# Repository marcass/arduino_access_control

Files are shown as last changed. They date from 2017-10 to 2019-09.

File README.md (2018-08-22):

# arduino_access_control
* Use arduino to control access to electrically actuated devices

## Components
* Electronically actuated device (garage door/door/or anything you want to access)
* WiFi in range
* Arduino as node/client (communicates to network using ESP8266 and [WIFIESP](https://github.com/bportaluri/WiFiEsp) arduino lib)
* Arduino runs this [MQTT lib](https://github.com/256dpi/arduino-mqtt)
* A master/server that runs mosquitto and a webserver

## How it works
1. Pincode gets sent to topic for door requests (either by pinpad, mqttclient, web interface, rfid device etc)
2. Pincode checked against database of allowed users
3. Response is sent to the node (allow or deny)
4. Relay is actuated and DB is updated

## User managment
Users added, modified and deleted via webpage in webserver (https://<servername/URL>)

## Maintenace
### Initial setup
* Update doorsetup.py to reflect doors you want to control
* run `python views.py <admin username> <admin password>` You get to choose what they are!
* Stop script then run via systemd (or whaterever process manager you use)
* Populate db via web interface (login usng credentials supplied above above)

### ssl certs
Letsencrypt cert needs to be renewed periodically:
1. Open port 80 on router to webserver (need to enable ipv6 for fritzbox to allow this then disable as ISP falls apart with IPv6 used)
2. run `sudo certbot renew`
3. Disable access via port 80

## Troubleshooting
### My uwsgi won't work (upstream timeout errors in /var/log/nginx/error.log)
* `# systemclt stop door`
* running (from python dir) $ uwsgi --ini uwsgi.py
* Ctrl+C that process after testing api is delivering
* `# systemctl start door`
This seems to work

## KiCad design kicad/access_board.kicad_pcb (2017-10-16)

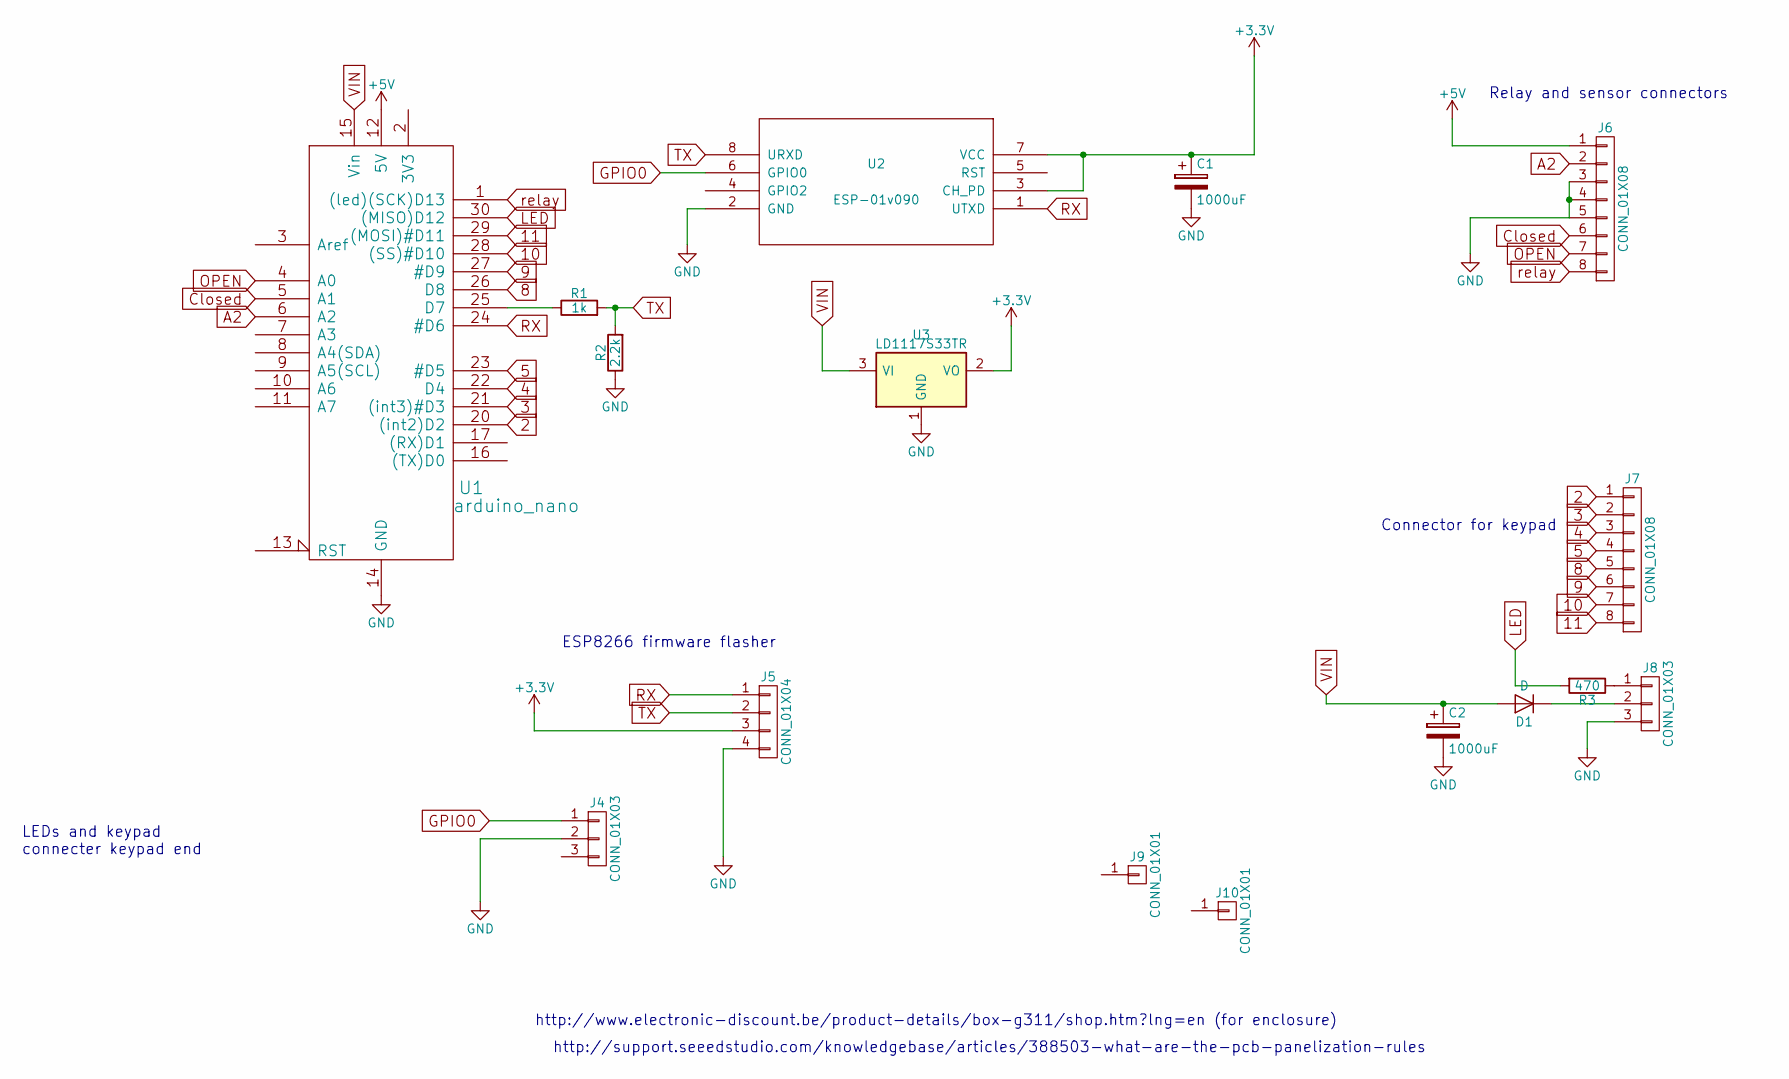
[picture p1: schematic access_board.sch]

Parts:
C1, C2: 1000uF; CP_Radial_D13.0mm_P5.00mm
D1: D; D_5W_P12.70mm_Horizontal
J4: CONN_01X03; Pin_Header_Straight_1x03_Pitch2.54mm
J5: CONN_01X04; Pin_Header_Straight_1x04_Pitch2.54mm
J6, J7: CONN_01X08; PhoenixContact_MCV-G_08x3.81mm_Vertical
J8: CONN_01X03; PhoenixContact_MCV-G_03x3.81mm_Vertical
J9, J10: CONN_01X01; MountingHole_3.2mm_M3_DIN965_Pad
R1: 1k; R_Axial_DIN0207_L6.3mm_D2.5mm_P10.16mm_Horizontal
R2: 2.2k; R_Axial_DIN0207_L6.3mm_D2.5mm_P10.16mm_Horizontal
R3: 470; R_Axial_DIN0207_L6.3mm_D2.5mm_P10.16mm_Horizontal
U1: arduino_nano; ArduinoNano
U2: ESP-01v090; ESP-01
U3: LD1117S33TR; TO-220_Vertical

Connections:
2: J7.1, U1.20 ((int2)D2)
3: J7.2, U1.21 ((int3)#D3)
4: J7.3, U1.22 (D4)
5: J7.4, U1.23 (#D5)
8: J7.5, U1.26 (D8)
9: J7.6, U1.27 (#D9)
10: J7.7, U1.28 ((SS)#D10)
11: J7.8, U1.29 ((MOSI)#D11)
+3V3: C1.1, J5.3, U2.3 (CH_PD), U2.7 (VCC), U3.2 (VO)
+5V: J6.1, U1.12 (5V)
A2: J6.2, U1.6 (A2)
Closed: J6.6, U1.5 (A1)
GND: C1.2, C2.2, J4.2, J5.4, J6.3, J6.4, J6.5, J8.3, R2.1, U1.14 (GND), U1.19 (GND), U2.2 (GND), U3.1 (GND)
GPIO0: J4.1, U2.6 (GPIO0)
LED: R3.2, U1.30 ((MISO)D12)
unnamed: D1.1 (K), J8.2
unnamed: J8.1, R3.1
unnamed: R1.1, U1.25 (D7)
OPEN: J6.7, U1.4 (A0)
RX: J5.1, U1.24 (#D6), U2.1 (UTXD)
TX: J5.2, R1.2, R2.2, U2.8 (URXD)
VIN: C2.1, D1.2 (A), U1.15 (Vin), U3.3 (VI)
relay: J6.8, U1.1 ((led)(SCK)D13)

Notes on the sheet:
ESP8266 firmware flasher
Connector for keypad
LEDs and keypad connecter keypad end
Relay and sensor connectors
http://www.electronic-discount.be/product-details/box-g311/shop.htm?lng=en (for enclosure)
http://support.seeedstudio.com/knowledgebase/articles/388503-what-are-the-pcb-panelization-rules

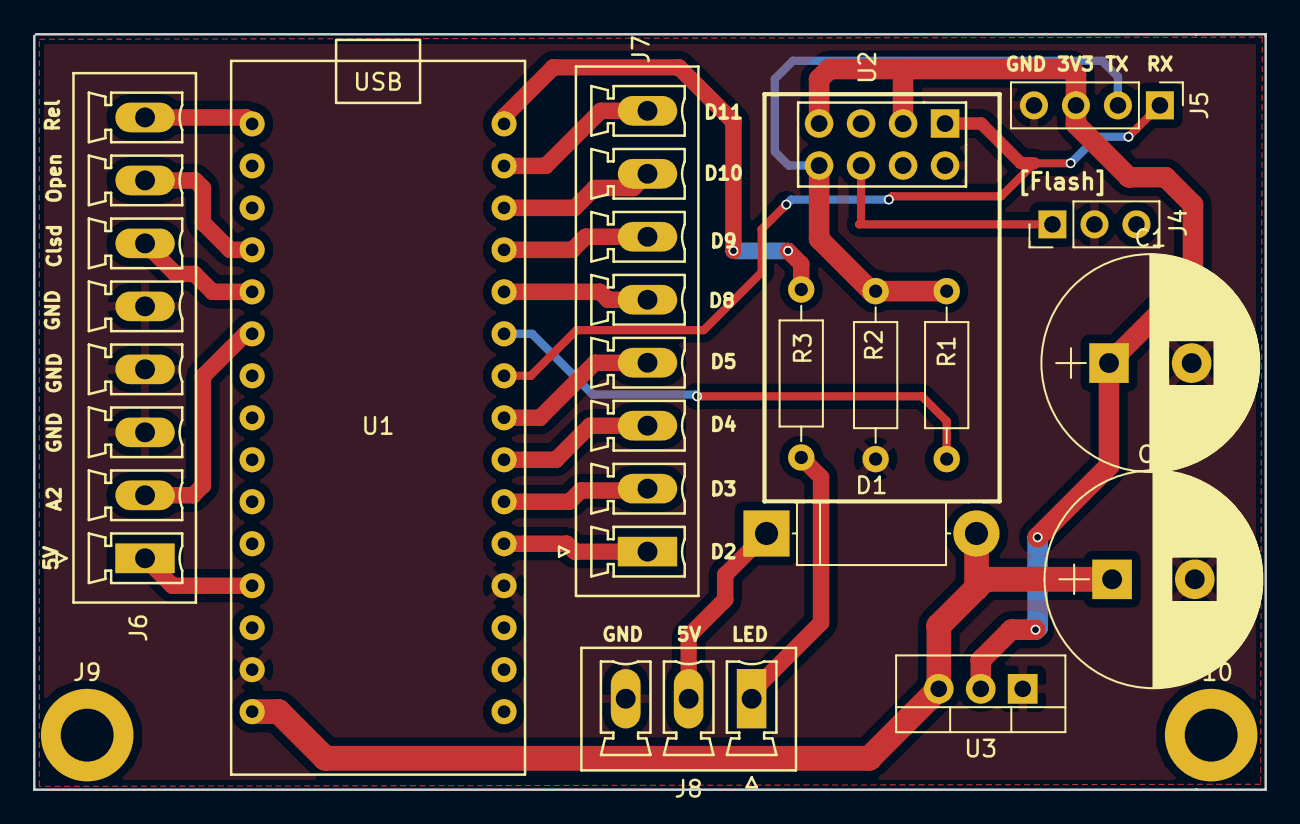
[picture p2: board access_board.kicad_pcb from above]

Board: 2 copper layers, 74.5 x 45.7 mm, 16 parts (0 on the bottom side), 23 nets.

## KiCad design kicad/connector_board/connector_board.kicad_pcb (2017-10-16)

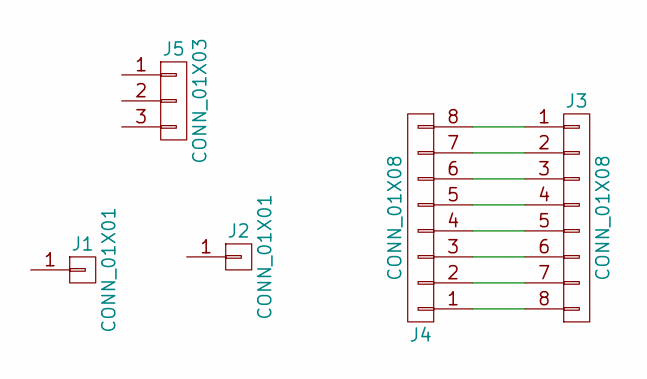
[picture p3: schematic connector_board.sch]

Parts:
J1, J2: CONN_01X01; MountingHole_3.7mm_Pad
J3: CONN_01X08; PhoenixContact_MCV-G_08x3.81mm_Vertical
J4: CONN_01X08; Pin_Header_Straight_1x08_Pitch2.54mm
J5: CONN_01X03; PhoenixContact_MCV-G_03x3.81mm_Vertical

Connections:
unnamed: J3.1, J4.8
unnamed: J3.2, J4.7
unnamed: J3.3, J4.6
unnamed: J3.4, J4.5
unnamed: J3.5, J4.4
unnamed: J3.6, J4.3
unnamed: J3.7, J4.2
unnamed: J3.8, J4.1

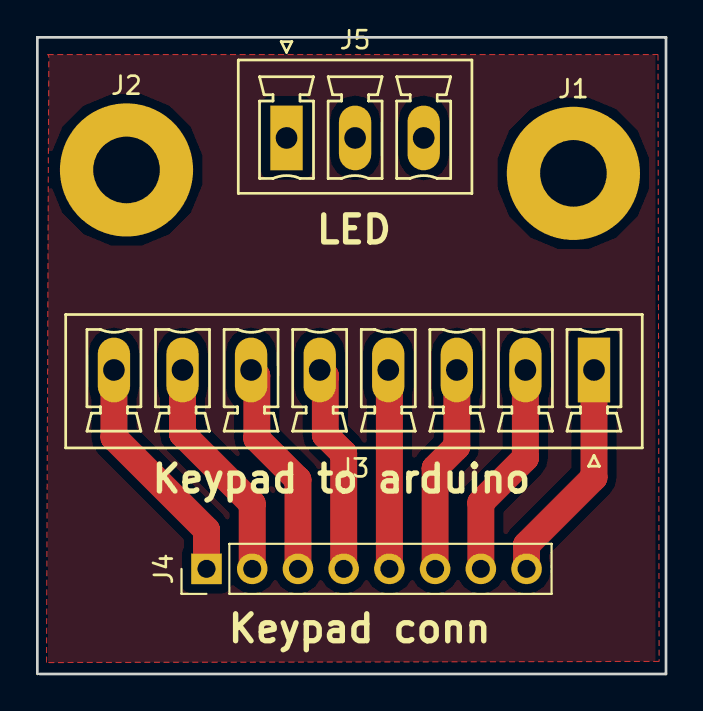
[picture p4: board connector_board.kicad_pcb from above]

Board: 2 copper layers, 34.9 x 35.4 mm, 5 parts (0 on the bottom side), 8 nets.

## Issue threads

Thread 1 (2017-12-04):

Arduino fails to connect to server

marcass, 2017-12-04:
Happens with low and unpredictable frequency. May have something to do with using alternative mqtt client to arduino itself (eg phone client)

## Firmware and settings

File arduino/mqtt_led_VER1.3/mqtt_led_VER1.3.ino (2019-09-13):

#include <SPI.h>
#include "WiFiEsp.h"
#include <Keypad.h>
//https://github.com/256dpi/arduino-mqtt
#include <MQTTClient.h>
#include <Adafruit_NeoPixel.h>

#define debug

const char DOOR[] = "bottomgarage";
const char ssid[] = "skibo";            // your network SSID (name)
const char pass[] = "r4bb1tshurtlegs";            // your network password
const char HOST[] = "192.168.0.152";
//char HOST[] = "nuc";

const char willTOPIC[] = "doors/offline/bottomgarage";
const char willMESS[] = "offline";

//const char USER[] = "";
//const char MOSQ_PASS[] = "";

const byte ROWS = 4; //four rows
const byte COLS = 4; //four columns
//define the symbols on the buttons of the keypads
char hexaKeys[ROWS][COLS] = {
  {'1','2','3','A'},
  {'4','5','6','B'},
  {'7','8','9','C'},
  {'*','0','#','D'}
};

/*           Row pin
 * 1 2 3 A | 6
 * 4 5 6 B | 7
 * 7 8 9 C | 8
 * * 0 # D | 9
 * ---------
 * 2 3 4 5 <- Col pin
 * Pins numbered form left to right when looking at keys on keypad
 * Need D6 and D7 for software serial
 *
 * byte rowPins[ROWS] = {6, 7, 8, 9}; //connect to the row pinouts of the keypad
 * byte colPins[COLS] = {2, 3, 4, 5}; //connect to the column pinouts of the keypad
 */
byte                  colPins[ROWS] = {8,9,10,11}; //connect to the row pinouts of the keypad
byte                  rowPins[COLS] = {2,3,4,5}; //connect to the column pinouts of the keypad
String                key_str = "";
bool                  sendKey = false;
bool                  looped = false;
unsigned long         pin_start = 0;
const unsigned long   KEY_THRESH = 30000; //30sec to put pin in
unsigned long         relay_time = 0;
const unsigned long   RELAY_TRIG = 300;
unsigned long         led_time = 0;
const unsigned long   LED_TIME = 3000; //3sec
unsigned long         INTERVAL = 50;  // the time we need to wait for led update
unsigned long         previousMillis = 0;
unsigned long         LED_CHANGE_TIME = 2000;
unsigned long         led_change_time;
unsigned long         loop_timer = millis();
const unsigned long   LOOP_THRESH = 100;
const byte            STATE_IDLE = 1;
const byte            STATE_TRIGGER = 2;
byte                  state = STATE_IDLE;
const int             RELAY = A2;
#define               LED 12
#define               SW_OPEN A0
#define               SW_CLOSED A1
// How many NeoPixels are attached to the Arduino?
#define               NUMPIXELS      24
char                  DOOR_PUB[] = "doors/request/bottomgarage";
char                  DOOR_SUB[] = "doors/response/bottomgarage";
char                  DOOR_STATE[] = "doors/status/bottomgarage";
//door states
const int             STATE_OPEN = 0;
const int             STATE_CLOSED = 1;
const int             STATE_UNKNOWN = 2;
int                   door_state = STATE_UNKNOWN;
int                   prev_door_state;
//led states
const byte            NOT_CONN = 3;
const byte            KEY_IN = 4;
const byte            DENIED = 5;
byte                  led_state = NOT_CONN;
byte                  new_led_state;
byte                  prev_led_state;
byte                  disp_pix = 0;
byte                  prev_disp_pix;

//initialize an instance of class NewKeypad
Keypad customKeypad = Keypad( makeKeymap(hexaKeys), rowPins, colPins, ROWS, COLS);

// When we setup the NeoPixel library, we tell it how many pixels, and which pin to use to send signals.
// Note that for older NeoPixel strips you might need to change the third parameter--see the strandtest
// example for more information on possible values.
Adafruit_NeoPixel pixels = Adafruit_NeoPixel(NUMPIXELS, LED, NEO_GRB + NEO_KHZ800);

// Emulate Serial1 on pins 6/7 if not present
// Set ESP8266 baud rate to 9600. You only need to do this once per device
//send "AT+UART_DEF=9600,8,1,0,0";
//set hardware serial to 115200, 
//set software serial baud to 9600;
#ifndef HAVE_HWSERIAL1
#include "SoftwareSerial.h"
SoftwareSerial Serial1(6, 7); // RX, TX
#endif

int status = WL_IDLE_STATUS;     // the Wifi radio's status

// Initialize the Ethernet client object
WiFiEspClient net;
MQTTClient client;

unsigned long lastMillis = 0;

void setup() {
  // initialize serial for debugging
  Serial.begin(115200);
  // initialize serial for ESP module
  // Set ESP8266 baud rate to 9600. You only need to do this once per device
  //send "AT+UART_DEF=9600,8,1,0,0";
  // toset software serial baud to 9600;
  // From now on, communicate with your device at 9600 baud.
  Serial1.begin(9600);
  //setup digital pins
  pinMode(RELAY, OUTPUT);
  digitalWrite(RELAY, LOW);
  pinMode(LED, OUTPUT);
  digitalWrite(LED, LOW);
  pinMode(SW_OPEN, INPUT_PULLUP);
  pinMode(SW_CLOSED, INPUT_PULLUP);
  // initialize ESP module
  WiFi.init(&Serial1);

  // MQTT brokers usually use port 8883 for secure connections.
  client.setWill(willTOPIC, willMESS, true, 0);
  client.begin(HOST, net);
  client.onMessage(messageReceived);
  
  connect();
  pixels.begin();
}


//void setWill(const char topic[]);
//void setWill(const char topic[], const char payload[]);
//void setWill(const char topic[], const char payload[], bool retained, int qos);
//void clearWill();

void connect(){
  // check for the presence of the shield
  if (WiFi.status() == WL_NO_SHIELD) {
    #ifdef debug
      Serial.println("WiFi shield not present");
    #endif
    // don't continue
    while (true);
  }

  // attempt to connect to WiFi network don't do in a while loop as it may time out
//  while ( status != WL_CONNECTED) {
  Serial.print("Attempting to connect to WPA SSID: ");
  Serial.println(ssid);
  // Connect to WPA/WPA2 network
  status = WiFi.begin(ssid, pass);
//  }
  #ifdef debug
    // you're connected now, so print out the data
    Serial.println("You're connected to the network");
    printWifiStatus();
  #endif
  Serial.print("\nconnecting...");
//  while (!client.connect(DOOR, USER, MOSQ_PASS)) {
  while (!client.connect("testdoor")) {
    Serial.print(".");
    delay(1000);
  }
//  client.connect(DOOR);
//  delay(1000);
//  client.setOptions(60, true, 1000);
  client.publish(willTOPIC, "online", true, 1);
  //boolean connect(const char clientId[], const char username[], const char password[]);
  //client.connect(DOOR, USER, MOSQ_PASS);
  //client.subscribe(DOOR_SUB, 1);
  while (!client.subscribe("doors/response/bottomgarage", 1)) {
    Serial.print("*");
    delay(1000);
  }
  new_led_state = state;
  //led_state = state;
  led_change_time = 0;
  manage_led();
}

void check_state(){
  //if SW_OPEN is LOW (and SW_CLOSED is HIGH) door is open and vice versa. Unkown if not in either of these
  int open_reed = digitalRead(SW_OPEN);
  int closed_reed = digitalRead(SW_CLOSED);
  if ((open_reed == LOW) && (closed_reed == HIGH)){
    door_state = STATE_OPEN;
  }
  else if ((open_reed == HIGH) && (closed_reed == LOW)){
    door_state = STATE_CLOSED;
  }
  else{
    door_state = STATE_UNKNOWN;
  }
  if (door_state != prev_door_state){
    char* doorStates[] = {"open", "closed", "unknown"};
    #ifdef debug
      Serial.print("Publishing state change to: ");
      Serial.println(doorStates[door_state]);
    #endif
    client.publish(DOOR_STATE, (String)doorStates[door_state], true, 1);
    prev_door_state = door_state;
    //manage_led();
  }
}

void send_pin(String pin){
  //boolean publish(const String &topic, const String &payload, bool retained, int qos);
  if (client.publish(DOOR_PUB, pin, false, 2)){
    #ifdef debug
      Serial.println("Send successful");
    #endif
  }else{
    #ifdef debug
      Serial.println("Send failed");
    #endif
  }
}

void keypadListen(){
  //timeout for keys not pressed
  if (millis() - pin_start > KEY_THRESH){
    if (key_str != ""){
      key_str = "";
      disp_pix = 0;
    }
  }
  char key = customKeypad.getKey();
  if (key){
    #ifdef debug
//      Serial.print("Currnet state for LED is "+(String)led_state);
      Serial.println("Changing to key in LED state");
    #endif
    led_state = KEY_IN;
    //reset timeout timer
    pin_start = millis();
    if(key == '#'){
      sendKey = true;
      disp_pix = 0;
    }else{
      key_str += key;
      #ifdef debug
        Serial.print("Pressed key is: ");
        Serial.println(key);
      #endif
      disp_pix = disp_pix + 3;      
    }
  }
  if (sendKey){
    #ifdef debug
      Serial.println(key_str);
    #endif
    send_pin(key_str);
    key_str = "";
    sendKey = false;
  }else{
    //do nothing and come back again
  }
}

void open_door(){
  #ifdef debug
    Serial.println("Opening door as requested");
  #endif
  if (relay_time == 0){
    relay_time = millis();
  }
  if (millis() - relay_time > RELAY_TRIG){
    digitalWrite(RELAY, LOW);
    relay_time = 0;
    state = STATE_IDLE;
    led_state = state;
  }else{
    digitalWrite(RELAY, HIGH);
  }
}


void set_led(int in_pix, int red, int green, int blue){
  for (int i = 0; i < in_pix; i++){
    pixels.setPixelColor(i, pixels.Color(red,green,blue));
  }
}

void manage_led(){
  switch (led_state){
    case NOT_CONN:
      set_led(NUMPIXELS, 20, 20, 20);
      break;
    case STATE_IDLE:
      set_led(NUMPIXELS, 0, 0, 0);
      set_led(2, 20, 0, 0);
      break;
    case KEY_IN:
      set_led(NUMPIXELS, 0, 0, 0);
      set_led(disp_pix, 0, 50, 0);
      prev_disp_pix = disp_pix;
      break;
    case STATE_TRIGGER:
      set_led(NUMPIXELS, 0, 50, 50);
      new_led_state = STATE_IDLE;
//      led_state = STATE_IDLE;
      led_change_time = 0;
      break;
    case DENIED:
      set_led(NUMPIXELS, 50, 0, 50);
      break;
  }
  pixels.show(); // This sends the updated pixel color to the hardware.
  prev_led_state = led_state;
}

void loop() {
  if(looped) {
    Serial.println("client is looping");
    looped = false;
  }
//  Serial.print("Led_state is ");
//  Serial.println(led_state);
  if (millis() - loop_timer > LOOP_THRESH) {
    client.loop();
//    loop_timer = millis();
//    looped = true;
  }
//  client.loop();
  //delay(100);
  //Serial.println(state);
  if (!client.connected()) {
    led_state = NOT_CONN;
    Serial.println("not connected....");
    connect();
  }
  switch (state){
    case STATE_IDLE:
      keypadListen();
      check_state();
      break;
    case STATE_TRIGGER:
      open_door();
      break;
  }
  //run led stuff
  if ((disp_pix != prev_disp_pix) or (led_state != prev_led_state)){
    //Serial.println("I'm managing hte LED");
    manage_led();
  }
  if (led_state == DENIED) {
    if (led_time == 0) {
      led_time = millis();
    }
    if (millis() - led_time > RELAY_TRIG) {
      new_led_state = STATE_IDLE;
//      led_state = STATE_IDLE;
      led_time = 0;
    }
  }
  //manage delay for changing led state
  if (new_led_state) {
    if (led_change_time == 0) {
      led_change_time = millis();
    }
    if (millis() - led_change_time > LED_CHANGE_TIME) {
      led_state = new_led_state;
      new_led_state = NULL;
    }
  }
  //check_state();
}

void messageReceived(String &topic, String &payload) {
//  Won't work with following serial prints: 
//  Serial.println("Receiving the payload");
//  Serial.println(payload);
  #ifdef debug
    Serial.println("incoming: " + topic + " - " + payload);
  #endif
  if (payload == "1"){
    state = STATE_TRIGGER;
    led_state = state;
  }else{
    led_state = DENIED;
    #ifdef debug
      Serial.println("no, open it yourself");
    #endif
  }
}

void printWifiStatus()
{
  // print the SSID of the network you're attached to
  Serial.print("SSID: ");
  Serial.println(WiFi.SSID());

  // print your WiFi shield's IP address
  IPAddress ip = WiFi.localIP();
  Serial.print("IP Address: ");
  Serial.println(ip);

  // print the received signal strength
  long rssi = WiFi.RSSI();
  Serial.print("Signal strength (RSSI):");
  Serial.print(rssi);
  Serial.println(" dBm");
}

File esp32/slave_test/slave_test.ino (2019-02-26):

// based on https://gist.github.com/yaqwsx/ac662c9b600ef39a802da0be1b25d32d
// 2018.07.14 jnogues@gmail.com, Jaume Nogués, rPrim Tech
// This sketch shows the use of 802.11 LR (Low Rate)
// slave.ino

#include <Arduino.h>
#include <WiFi.h>
#include <WiFiUdp.h>
#include <esp_wifi.h>

const char* ssid = "kkkkk";//AP ssid
const char* password = "12345678";//AP password

WiFiUDP udp;

const char *toStr( wl_status_t status ) {
    switch( status ) {
    case WL_NO_SHIELD: return "No shield";
    case WL_IDLE_STATUS: return "Idle status";
    case WL_NO_SSID_AVAIL: return "No SSID avail";
    case WL_SCAN_COMPLETED: return "Scan compleded";
    case WL_CONNECTED: return "Connected";
    case WL_CONNECT_FAILED: return "Failed";
    case WL_CONNECTION_LOST: return "Connection lost";
    case WL_DISCONNECTED: return "Disconnected";
    }
    return "Unknown";
}

void setup() {
    Serial.begin( 115200 );
    Serial.println( "Slave" );
    pinMode(5, OUTPUT);//bultin Led, for debug

    //We start STA mode with LR protocol
    //This ssid is not visible whith our regular devices
    WiFi.mode( WIFI_STA );//for STA mode
    //if mode LR config OK
    int a= esp_wifi_set_protocol( WIFI_IF_STA, WIFI_PROTOCOL_LR );
    if (a==0)
    {
      Serial.println(" ");
      Serial.print("Error = ");
      Serial.print(a);
      Serial.println(" , Mode LR OK!");
    }
    else//if some error in LR config
    {
      Serial.println(" ");
      Serial.print("Error = ");
      Serial.print(a);
      Serial.println(" , Error in Mode LR!");
    }

    WiFi.begin(ssid, password);//this ssid is not visible

    //Wifi connection, we connect to master
    while (WiFi.status() != WL_CONNECTED)
    {
      delay(500);
      Serial.print(".");
    }

    Serial.println("WiFi connected");
    Serial.print("IP address: ");
    Serial.println(WiFi.localIP());

    udp.begin( 8888 );
}

void loop() {
     //problems whith connection
    if ( WiFi.status() != WL_CONNECTED )
    {
        Serial.println( "|" );
        int tries = 0;
        WiFi.begin( ssid, password );
        while( WiFi.status() != WL_CONNECTED ) {
            tries++;
            if ( tries == 5 )
                return;
            Serial.println( toStr( WiFi.status() ) );
            delay( 1000 );
        }
        Serial.print( "Connected " );
        Serial.println( WiFi.localIP() );
    }
    udp.beginPacket( { 192, 168, 4, 255 }, 8888 );//send a broadcast message
    udp.write( 'b' );//the payload
    digitalWrite(5, !digitalRead(5));

    if ( !udp.endPacket() ){
        Serial.println("NOT SEND!");
        delay(100);
        ESP.restart(); // When the connection is bad, the TCP stack refuses to work
    }
    else{
          Serial.println("SEND IT!!");
    }

    delay( 1000 );//wait a second for the next message
//    //if connection OK, execute command 'b' from master
//    int size = udp.parsePacket();
//    if ( size == 0 )
//        return;
//    char c = udp.read();
//    if ( c == 'b' ){
//        digitalWrite(5, !digitalRead(5));//toggle Led
//        Serial.println("RECEIVED!");
//        Serial.println(millis());
//    }
//    udp.flush();
}

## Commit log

2017-09-07 updated arduino sketch and added max's flask server example
2017-09-15 started pcb dev
    [access_board.kicad_pcb, access_board.sch]
2017-09-18 schematic update
    [access_board.sch]
2017-09-21 arduino tests
2017-09-25 adding sockets functionality - tested and working
2017-09-25 low memmory on arduino in production and connection failing for some reason
    [KeypadTest.ino, production.ino, websocketSSl.ino.ino]
2017-09-26 discarded ArduinoJSON due to memory footprint
2017-10-04 arduino mqtt done
2017-10-05 updated schmeatic
    [access_board.sch]
2017-10-05 refining for broker connection
    [mqtt.ino]
2017-10-06 tested and working arduino script
2017-10-06 door states added
    [access_board.sch]
2017-10-10 updated kicad schematic
    [access_board.sch]
2017-10-11 pcb layout
    [access_board.kicad_pcb, access_board.sch]
2017-10-11 more pcb stuff
    [access_board.kicad_pcb, access_board.sch]
2017-10-12 added neopixel and continued with pdb
    [access_board.kicad_pcb, access_board.sch]
2017-10-12 updated pcb
    [access_board.kicad_pcb]
2017-10-14 changed qos level to 0 due to problems with arduino mqtt lib at qos 2
    [mqtt.ino]
2017-10-15 updated caps and checked diode size on board, started sketch mod for leds
    [access_board.kicad_pcb, access_board.sch]
2017-10-16 added connector board as a different kicad file
    [access_board.kicad_pcb, access_board.sch, connector_board.kicad_pcb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]
2017-10-16 setting up sketch for pixels and updated connector board
    [access_board.kicad_pcb, connector_board.kicad_pcb]
2017-10-17 leds coded for sketch, now need to test
2017-11-03 entered diode value
    [access_board.sch]
2017-11-07 removed most of debugging prints from api
2017-11-08 removed debugging prints from api
2017-12-04 reaarranged some arduino stuff
2017-12-04 got leds working - needed timer to cause delay so lib could catch up
2018-02-27 fixed message received problem via mqtt
    [mqtt_led_VER1.3.ino]
2018-05-09 getting mounted sorted slowly
2018-06-16 needed threads
2018-06-16 removed debugging prints
2018-06-18 needed more threads for wsgi and removed some debug prints
2018-07-22 combined boiler and door stuff
    [furnace_control.kicad_pcb, furnace_control.sch]
2018-08-03 missed brackets
2018-08-06 updated readmen and started on esp32 code
2018-08-06 route-by-role concept ready for testing, sensor db established, attempt at using https for esp32
2018-08-07 arduinohttpclient won't work with esp32
2018-08-08 starting to test client on esp32
2018-08-08 RP update for sensors db
2018-08-08 working route for a sensor tested with curl
2018-08-08 getting data in from esp32
2018-08-08 non ssl arduino sketch working
2019-02-02 getting temps into influx, removed print lines
2019-02-04 esp32 LR tests
2019-02-26 range testing lr connection on esp32
2019-08-10 publishing status and updated LWT
    [furnace_control.kicad_pcb, furnace_control.sch]
2019-09-13 given up on arduino and esp8266
